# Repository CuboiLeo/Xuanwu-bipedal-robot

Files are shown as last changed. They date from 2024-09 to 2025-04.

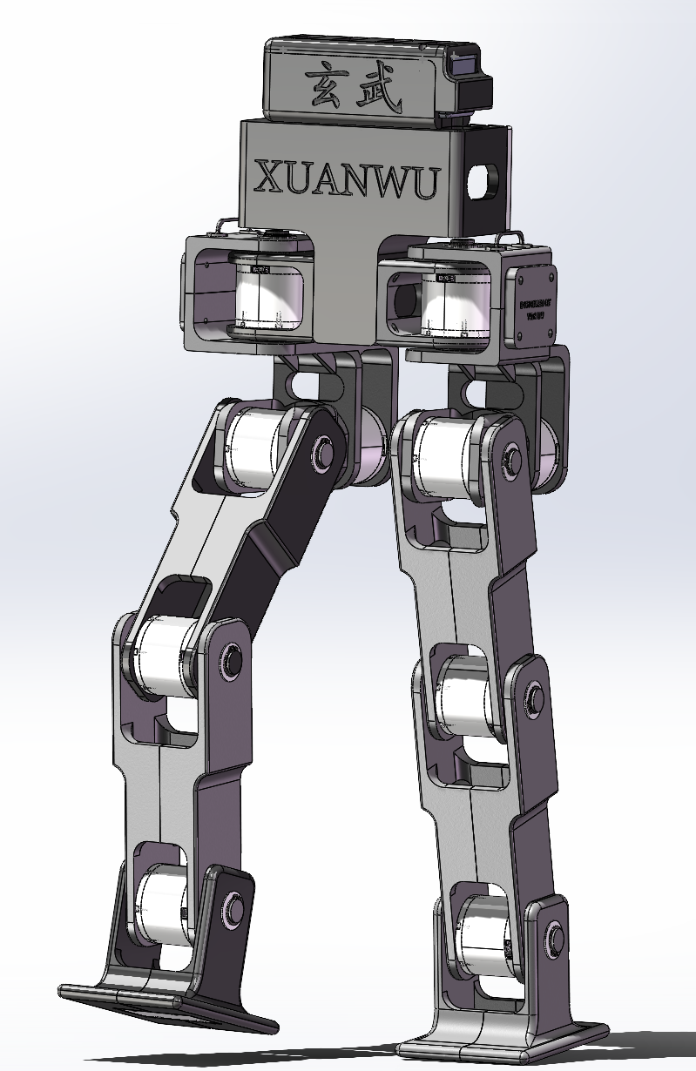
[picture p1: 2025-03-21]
media/image/CAD/Xuanwu v3.png

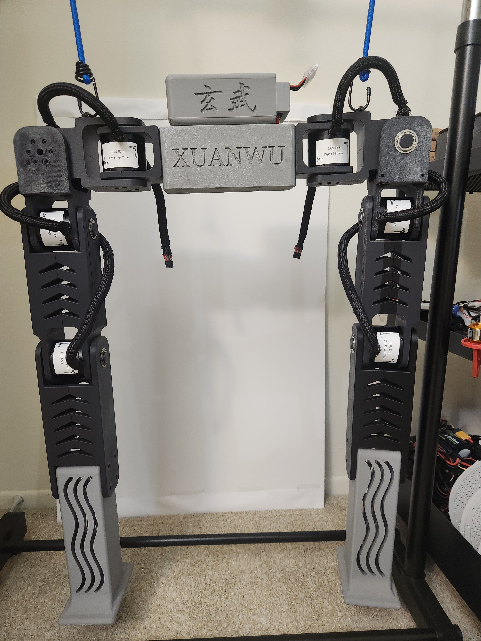
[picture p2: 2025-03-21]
media/image/Robot/Xuanwu v1.jpg

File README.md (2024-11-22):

# Xuanwu-bipedal-robot

This is an open-source bipedal robot project created by Yuxi Liu, aim to serve as a platform for testing various control algorithms

## Project hierarchy

This project contains three subfolders

- CAD - contains CAD files for parts of the robot, see CAD/README.md for detailed BoM and assembly guide
- source_code - contains code that the robot runs, see source_code/README.md for detailed introduction of code base structure
- media - contains media files such as video snippet of the robot, see media/README.md for more details

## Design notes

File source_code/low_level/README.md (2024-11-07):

# This folder is for the STM32H723 dev board

## IMPORTANT - If the project is regenerated using STM32CubeMX
You will see many errors if you rebuild the project in Keil, this is because STM32CubeMX uses RVDS for freeRTOS. To fix this, follow the following steps
1. Copy the GCC folder at the current directory
2. Paste it under ./Xuanwu_bipedal_robot/Middlewares/Third_Party/FreeRTOS/Source/portable, where you will see the STM32CubeMX generated RVDS and MemMang folders
3. Go to Keil, on the project tree on the left, find the last port.c file under Middlewares/FreeRTOS folder, right click and remove it
4. Go to Options for Target (magic wand icon in the tools menu), under C/C++, remove the RVDS/ARM_CM4F folder from the Include Paths
5. Build the project, there should (hopefully) be no more errors

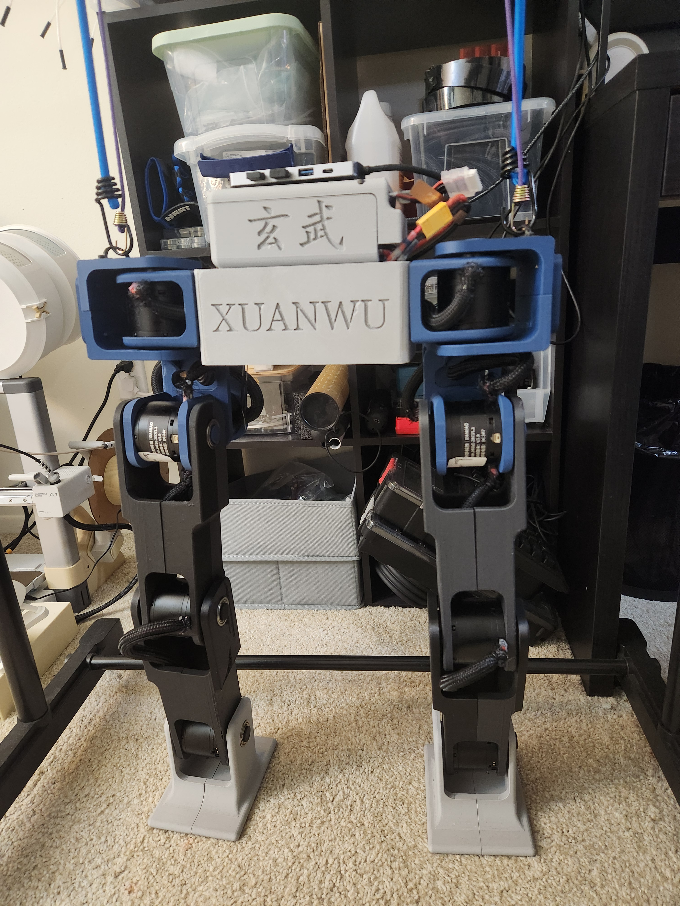
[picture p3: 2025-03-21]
media/image/Robot/Xuanwu v2.jpg

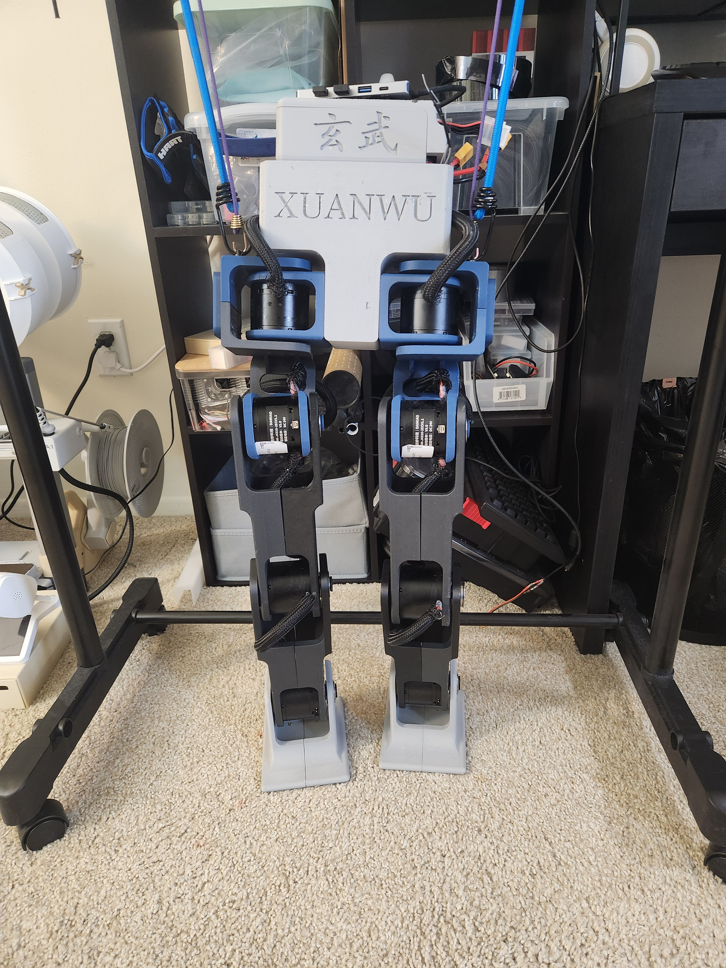
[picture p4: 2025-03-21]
media/image/Robot/Xuanwu v3.jpg

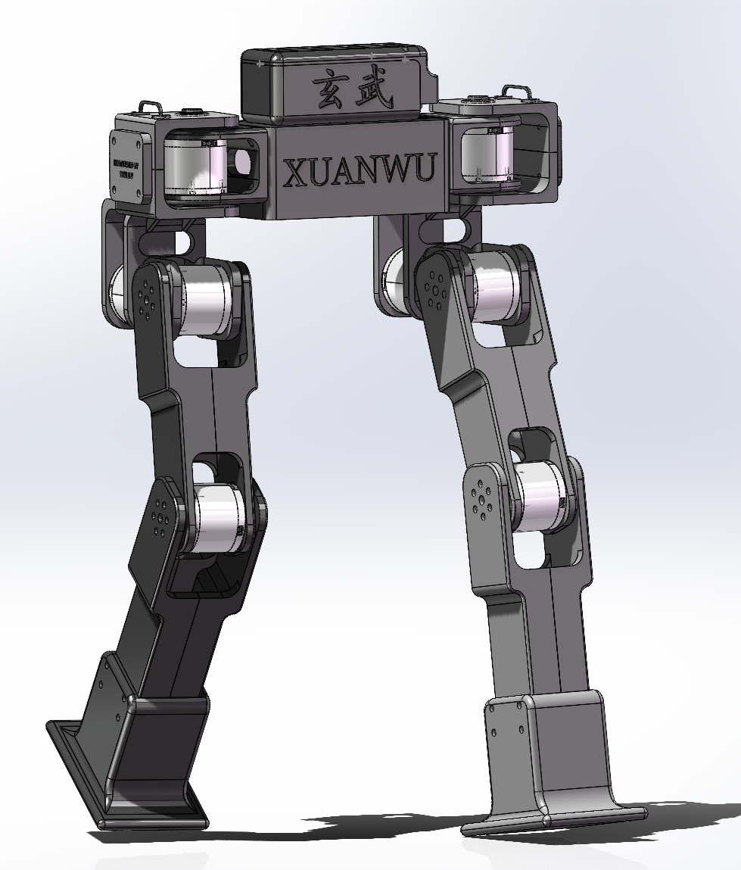
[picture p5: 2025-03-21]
media/image/CAD/Xuanwu v2.png

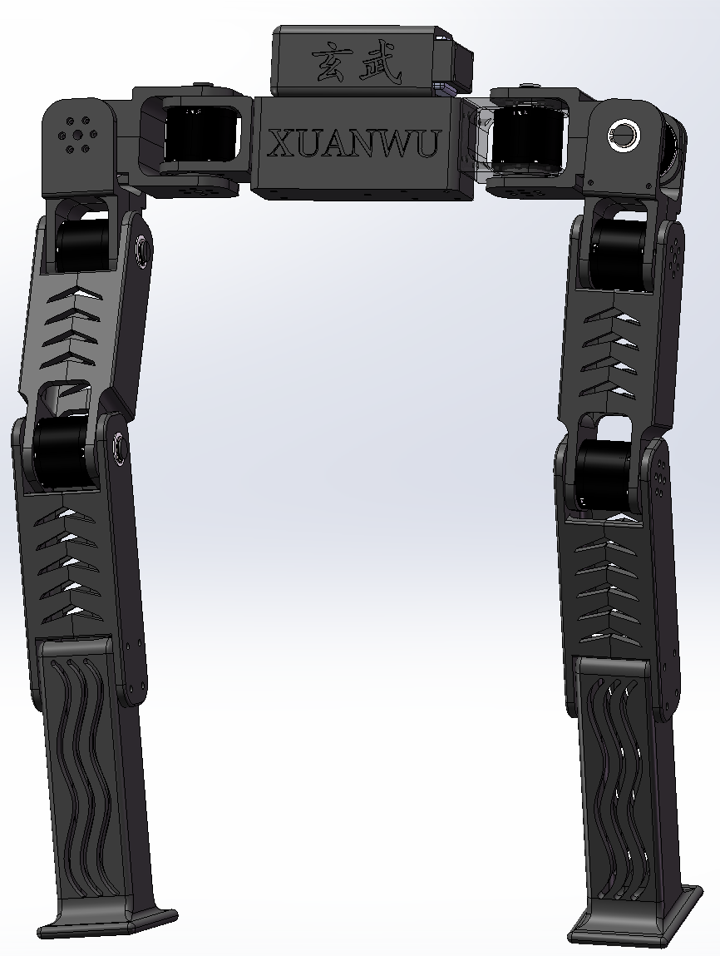
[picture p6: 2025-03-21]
media/image/CAD/Xuanwu v1.png

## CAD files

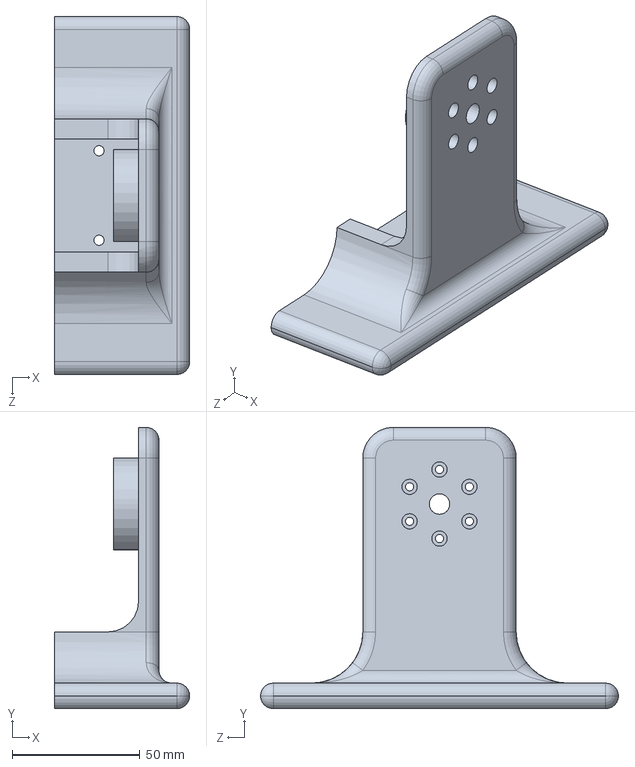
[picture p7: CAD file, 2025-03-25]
CAD/Leg/Divided Parts for Printing/DM-J4310 Foot Connector 1.SLDPRT
52.9 x 110.0 x 140.0 mm

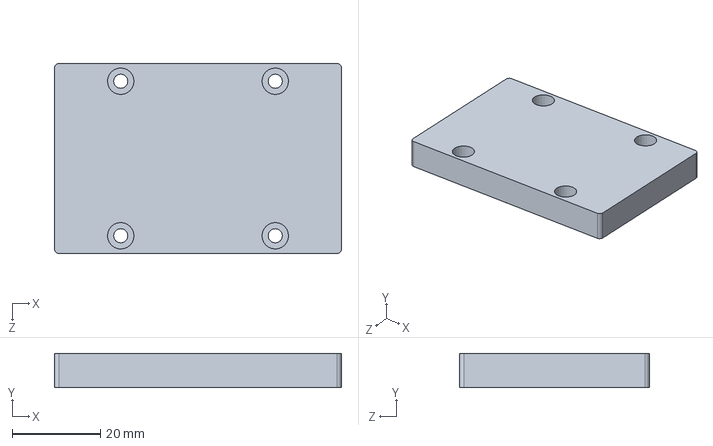
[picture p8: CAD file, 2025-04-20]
CAD/Leg/DM-J4310 Foot Joint Board.SLDPRT
65.0 x 7.80 x 43.0 mm

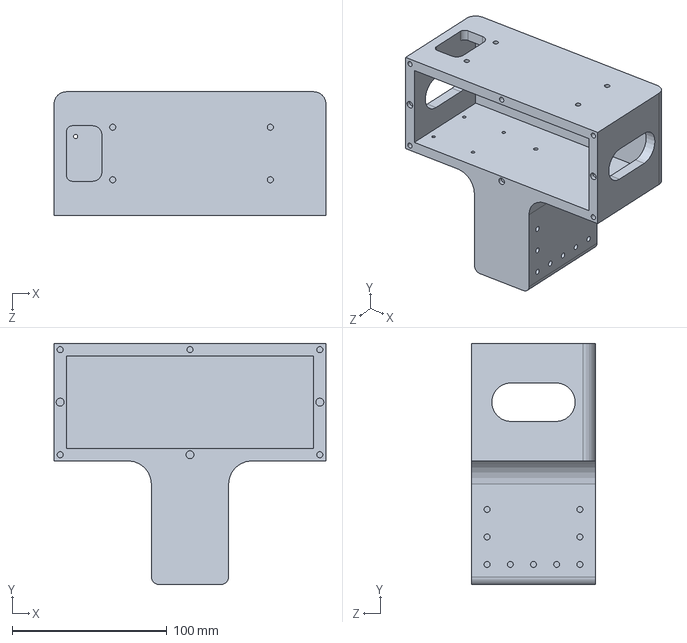
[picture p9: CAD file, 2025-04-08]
CAD/Main Control/Central Connector Module.SLDPRT
176.0 x 156.0 x 80.0 mm

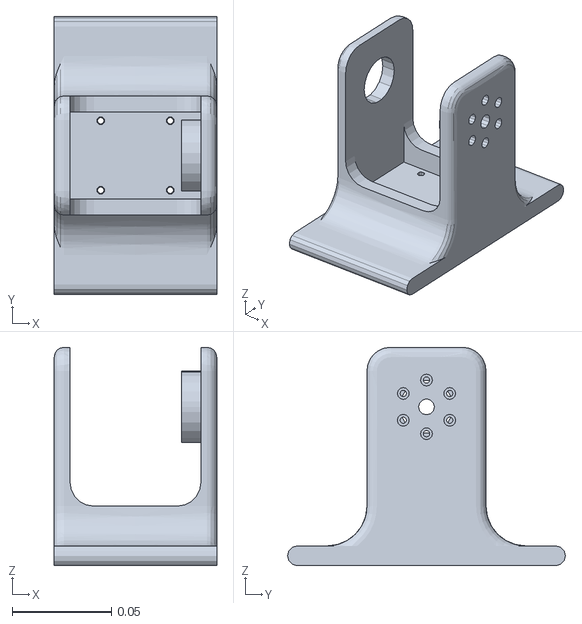
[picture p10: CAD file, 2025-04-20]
source_code/simulation/model/meshes/link_5.STL
0.0819 x 0.14 x 0.11

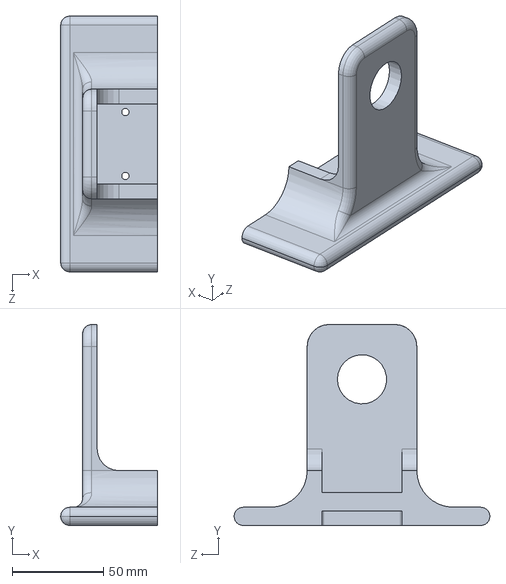
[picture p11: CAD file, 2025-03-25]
CAD/Leg/Divided Parts for Printing/DM-J4310 Foot Connector 2.SLDPRT
52.9 x 110.0 x 140.0 mm

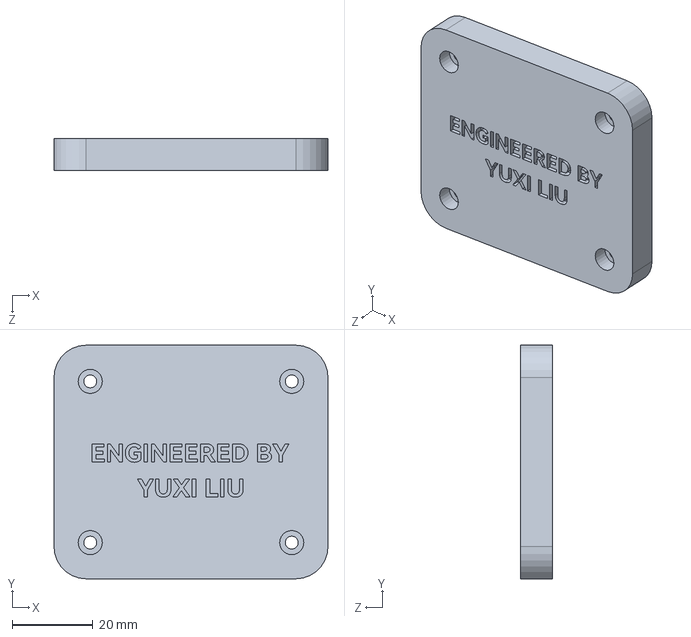
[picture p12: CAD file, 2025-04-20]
CAD/Leg/DM-J4310 Hip Roll Joint Board.SLDPRT
68.0 x 58.0 x 8.00 mm

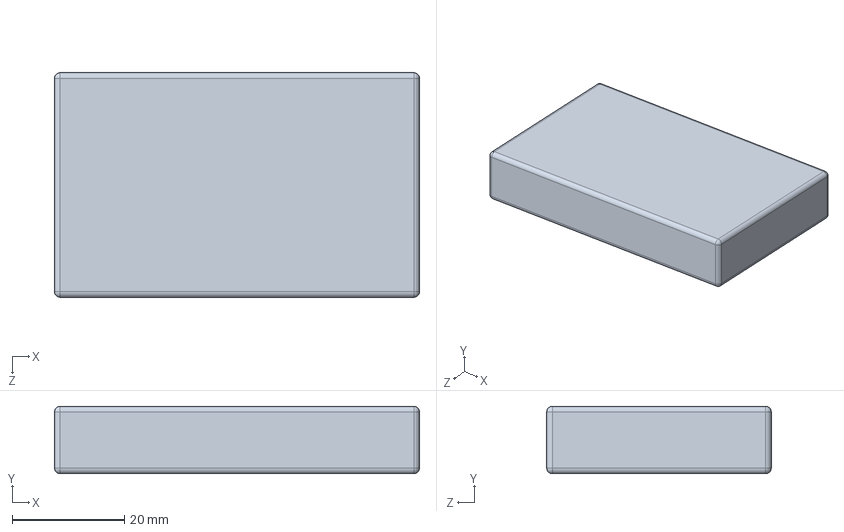
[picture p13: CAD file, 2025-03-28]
CAD/Main Control/Wireless Debugger.SLDPRT
65.0 x 12.0 x 40.0 mm

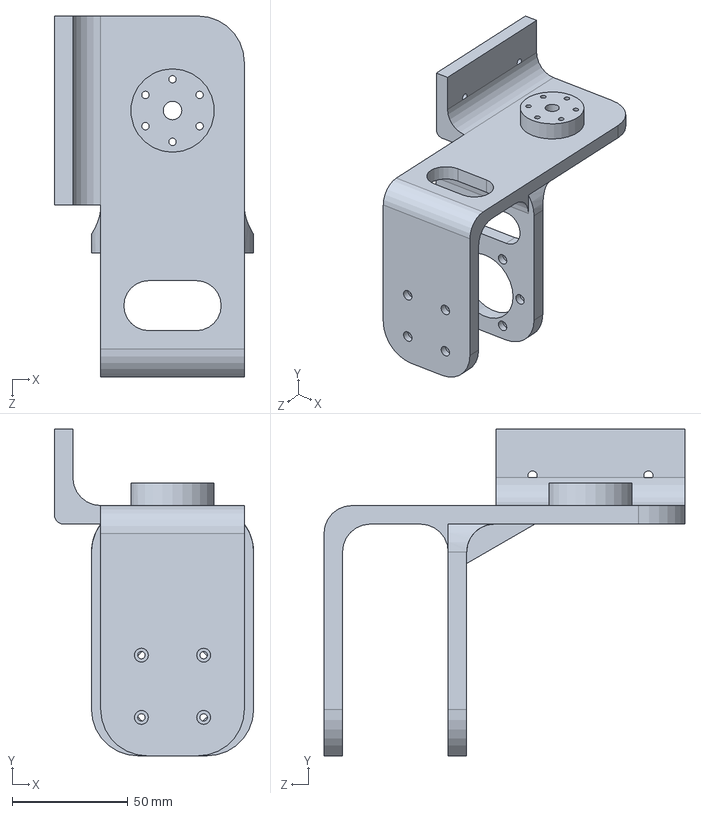
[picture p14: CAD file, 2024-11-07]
CAD/Leg/Divided Parts for Printing/DM-J4310 Hip Roll Connector Right 2.SLDPRT
86.0 x 140.9 x 155.8 mm

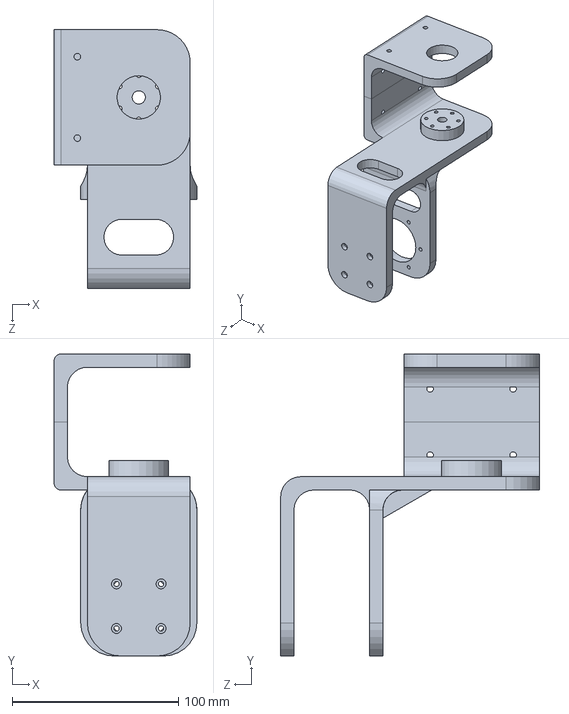
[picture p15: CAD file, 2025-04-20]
CAD/Leg/DM-J4310 Hip Roll Connector Right.SLDPRT
86.0 x 181.9 x 155.8 mm

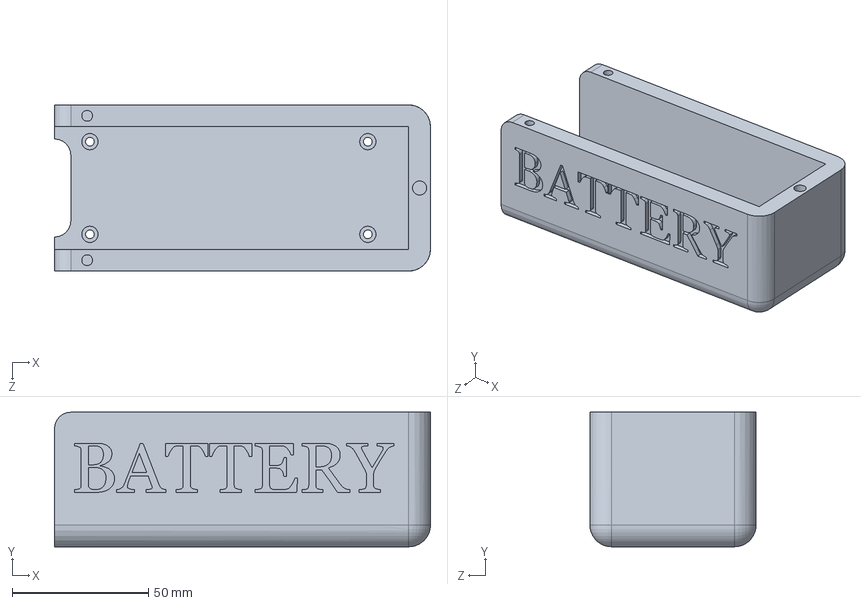
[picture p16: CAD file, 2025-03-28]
CAD/Main Control/Battery Case.SLDPRT
138.0 x 49.4 x 61.0 mm

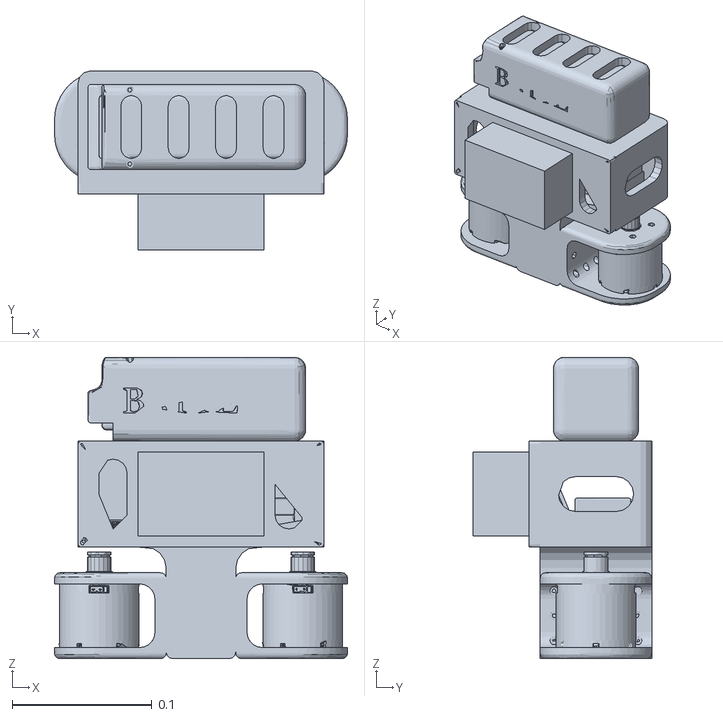
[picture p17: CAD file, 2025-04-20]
source_code/simulation/model/meshes/base_link.STL
0.21 x 0.128 x 0.216

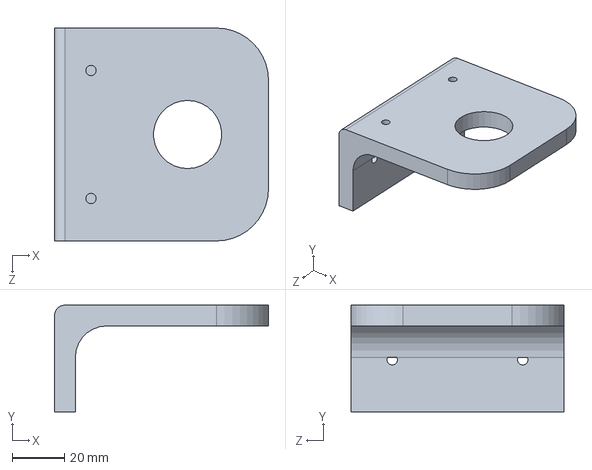
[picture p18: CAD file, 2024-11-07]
CAD/Leg/Divided Parts for Printing/DM-J4310 Hip Roll Connector Right 1.SLDPRT
82.0 x 41.0 x 81.6 mm

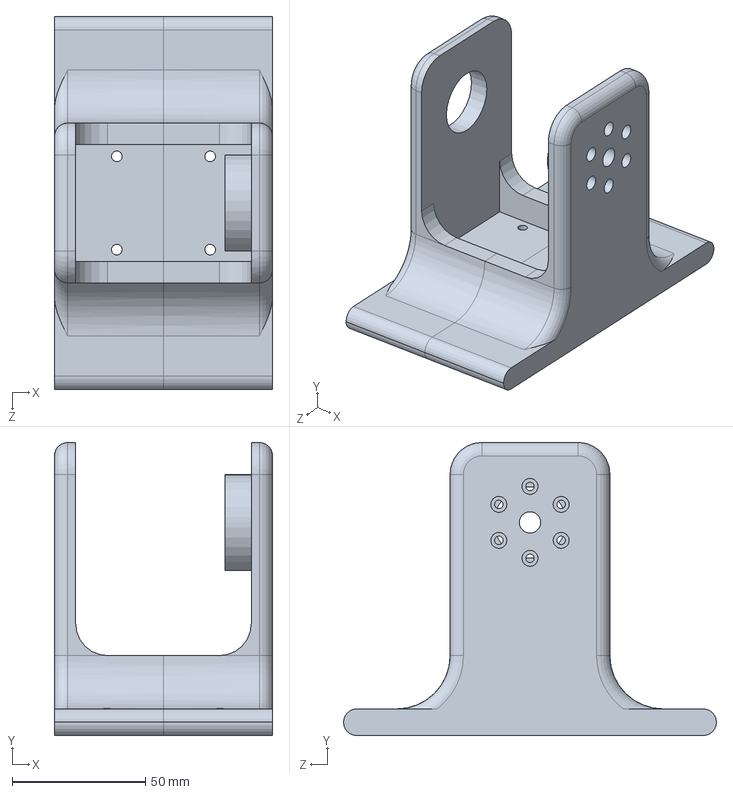
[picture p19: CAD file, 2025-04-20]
CAD/Leg/Foot Connector.SLDPRT
81.9 x 110.0 x 140.0 mm

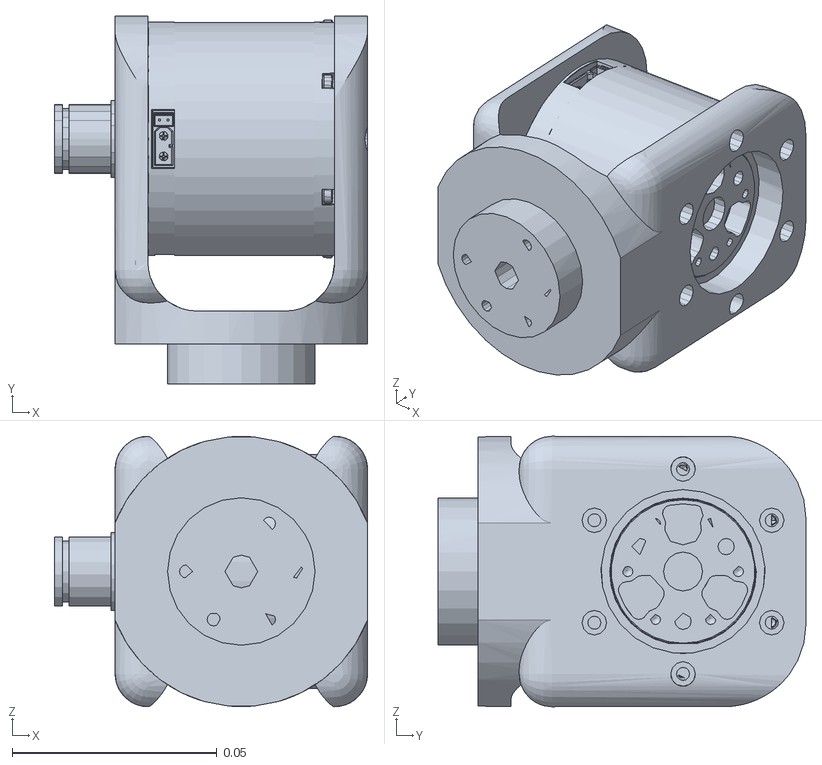
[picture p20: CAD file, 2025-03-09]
source_code/simulation/model/meshes/link_2.STL
0.0764 x 0.0898 x 0.066

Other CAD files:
CAD/Leg/Leg_Assem.SLDASM
source_code/simulation/model/meshes/link_10.STL
CAD/Main Control/CtrBoard Back Case.sldprt
CAD/Leg/Divided Parts for Printing/DM-J4310 Hip Roll Connector Left 1.SLDPRT
CAD/Leg/Bearing 17_26_5.SLDPRT
CAD/Leg/DM-J4310 Hip Pitch Connector.SLDPRT
CAD/Leg/DM-J4310 Hip Roll Connector Left.SLDPRT
CAD/Leg/DM-J4310 Hip Yaw Connector.SLDPRT
CAD/Leg/DM-J4310 Knee Pitch Connector.SLDPRT
CAD/Leg/Divided Parts for Printing/DM-J4310 Hip Roll Connector Left 2.SLDPRT
CAD/Leg/Divided Parts for Printing/DM-J4310 Knee Pitch Connector 1.SLDPRT
CAD/Leg/Divided Parts for Printing/DM-J4310 Knee Pitch Connector 2.SLDPRT
CAD/Leg/Hip Handle.SLDPRT
CAD/Main Control/6S Battery.SLDPRT
CAD/Main Control/Battery Case Cap.SLDPRT
CAD/Main Control/Central Connector Module Closing.SLDPRT
CAD/Main Control/CtrBoard Front Case.sldprt
CAD/Main Control/Orin Subs.SLDPRT
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

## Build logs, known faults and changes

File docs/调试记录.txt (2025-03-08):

2025/03/07 LIP模型
LIP模型假设腿无重量，实机调试时需要转移ZMP至支撑脚的convex hull后再迈下一步。
同时因最后输出为摆动腿的目标坐标，需要通过逆运动学得到期望的关节角度。然而双足的逆运动学（如果使用数值求解）常常只能近似，最终造成落点位置不精确。

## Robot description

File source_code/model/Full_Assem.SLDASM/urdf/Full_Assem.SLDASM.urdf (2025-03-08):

<?xml version="1.0" encoding="utf-8"?>
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
<robot name="Full_Assem.SLDASM">
  <link name="base_link">
    <inertial>
      <origin xyz="0.001 0 0.07" rpy="0 0 0" />
      <mass value="1.894" />
      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
    </inertial>
    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
  </link>
  <link name="link_1">
    <inertial>
      <origin xyz="-0.08 -0.06 -0.074" rpy="0 0 0" />
      <mass value="0.547" />
      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
    </inertial>
    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
  </link>
  <joint name="joint_1" type="revolute">
    <origin xyz="0 0 0" rpy="0 0 0" />
    <parent link="base_link" />
    <child link="link_1" />
    <axis xyz="0 0 1" />
    <limit lower="-0.5" upper="0.5" effort="7" velocity="12" />
  </joint>
  <link name="link_2">
    <inertial>
      <origin xyz="-0.073 -0.006 -0.111" rpy="0 0 0" />
      <mass value="0.378" />
      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
    </inertial>
    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
  </link>
  <joint name="joint_2" type="revolute">
    <origin xyz="0 0 0" rpy="0 0 0" />
    <parent link="link_1" />
    <child link="link_2" />
    <axis xyz="0 1 0" />
    <limit lower="-0.7" upper="0.7" effort="7" velocity="12" />
  </joint>
  <link name="link_3">
    <inertial>
      <origin xyz="-0.072 -0.001 -0.261" rpy="0 0 0" />
      <mass value="0.436" />
      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
    </inertial>
    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
  </link>
  <joint name="joint_3" type="revolute">
    <origin xyz="0 0 0" rpy="0 0 0" />
    <parent link="link_2" />
    <child link="link_3" />
    <axis xyz="1 0 0" />
    <limit lower="-0.25" upper="1.57" effort="7" velocity="12" />
  </joint>
  <link name="link_4">
    <inertial>
      <origin xyz="-0.072 -0.001 -0.441" rpy="0 0 0" />
      <mass value="0.436" />
      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
    </inertial>
    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
  </link>
  <joint name="joint_4" type="revolute">
    <origin xyz="0 0 0" rpy="0 0 0" />
    <parent link="link_3" />
    <child link="link_4" />
    <axis xyz="1 0 0" />
    <limit lower="-1.57" upper="1.57" effort="7" velocity="12" />
  </joint>
  <link name="link_5">
    <inertial>
      <origin xyz="-0.071 -0.001 -0.524" rpy="0 0 0" />
      <mass value="0.105" />
      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
    </inertial>
    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
  </link>
  <joint name="joint_5" type="revolute">
    <origin xyz="0 0 0" rpy="0 0 0" />
    <parent link="link_4" />
    <child link="link_5" />
    <axis xyz="1 0 0" />
    <limit lower="-1.57" upper="1.57" effort="7" velocity="12" />
  </joint>
  <link name="link_6">
    <inertial>
      <origin xyz="0.08 -0.06 -0.074" rpy="0 0 0" />
      <mass value="0.547" />
      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
    </inertial>
    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
  </link>
  <joint name="joint_6" type="revolute">
    <origin xyz="0 0 0" rpy="0 0 0" />
    <parent link="base_link" />
    <child link="link_6" />
    <axis xyz="0 0 1" />
    <limit lower="-0.5" upper="0.5" effort="7" velocity="12" />
  </joint>
  <link name="link_7">
    <inertial>
      <origin xyz="0.073 -0.006 -0.111" rpy="0 0 0" />
      <mass value="0.378" />
      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
    </inertial>
    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
  </link>
  <joint name="joint_7" type="revolute">
    <origin xyz="0 0 0" rpy="0 0 0" />
    <parent link="link_6" />
    <child link="link_7" />
    <axis xyz="0 1 0" />
    <limit lower="-0.7" upper="0.7" effort="7" velocity="12" />
  </joint>
  <link name="link_8">
    <inertial>
      <origin xyz="0.072 -0.001 -0.261" rpy="0 0 0" />
      <mass value="0.436" />
      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
    </inertial>
    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
  </link>
  <joint name="joint_8" type="revolute">
    <origin xyz="0 0 0" rpy="0 0 0" />
    <parent link="link_7" />
    <child link="link_8" />
    <axis xyz="1 0 0" />
    <limit lower="-0.25" upper="1.57" effort="7" velocity="12" />
  </joint>
  <link name="link_9">
    <inertial>
      <origin xyz="0.072 -0.001 -0.441" rpy="0 0 0" />
      <mass value="0.436" />
      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
    </inertial>
    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
  </link>
  <joint name="joint_9" type="revolute">
    <origin xyz="0 0 0" rpy="0 0 0" />
    <parent link="link_8" />
    <child link="link_9" />
    <axis xyz="1 0 0" />
    <limit lower="-1.57" upper="1.57" effort="7" velocity="12" />
  </joint>
  <link name="link_10">
    <inertial>
      <origin xyz="0.071 -0.001 -0.524" rpy="0 0 0" />
      <mass value="0.105" />
      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
    </inertial>
    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
  </link>
  <joint name="joint_10" type="revolute">
    <origin xyz="0 0 0" rpy="0 0 0" />
    <parent link="link_9" />
    <child link="link_10" />
    <axis xyz="1 0 0" />
    <limit lower="-1.57" upper="1.57" effort="7" velocity="12" />
  </joint>
</robot>

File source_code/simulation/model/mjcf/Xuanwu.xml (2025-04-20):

<mujoco model="Xuanwu">
  <option>
    <flag multiccd="enable"/>
  </option>
  <compiler angle="radian" meshdir="../meshes/" eulerseq="zyx"/>
  <size njmax="500" nconmax="100" />
  <option timestep="0.001" iterations="50" solver="PGS" gravity="0 0 -9.81" noslip_iterations="20">
  <flag sensornoise="enable" frictionloss="enable"/>
  </option>
  <default>
      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
  </default>
  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

  <worldbody>
    <light directional="true" diffuse=".4 .4 .4" specular="0.1 0.1 0.1" pos="0 0 5.0" dir="0 0 -1" castshadow="false"/>
    <light directional="true" diffuse=".6 .6 .6" specular="0.2 0.2 0.2" pos="0 0 4" dir="0 0 -1"/>
    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
    
    <body name="base_link" pos="0 0 0.556">
      <freejoint/>
      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
      <inertial pos="0.000934 -0.004880 0.069827" mass="2.016243" diaginertia="0.0251293 0.0206152 0.00691741"/>
      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
      <body name="link_1" pos="-0.073035 -1.4472E-05 -0.00095242" quat="1 0 0 0">
        <inertial pos="-0.006856 -0.062152 -0.076118" mass="0.504" diaginertia="0.00703726 0.0069965 0.000427238"/>
        <joint name="joint_1" pos="0 0 0" axis="0 0 1" range="-0.5 0.5" damping="0.01" frictionloss="0.01" armature="0.01" limited="true"/>
        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
        <body name="link_2" pos="4.9294E-05 -0.083183 -0.11003" quat="1 0 0 0">
          <inertial pos="-0.000218 0.076679 0.000024" mass="0.390" diaginertia="0.002479 0.00246102 0.000115979"/>
          <joint name="joint_2" pos="0 0 0" axis="0 1 0" range="-0.7 0.7" damping="0.01" frictionloss="0.01" armature="0.01" limited="true"/>
          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
          <body name="link_3" pos="0.00098795 0.082032 2.035E-05" quat="1 0 0 0">
            <inertial pos="-0.000371 -0.000049 -0.144385" mass="0.481" diaginertia="0.011859 0.0117753 0.000262696"/>
            <joint name="joint_3" pos="0 0 0" axis="1 0 0" range="-0.25 1.57" damping="0.01" frictionloss="0.01" armature="0.01" limited="true"/>
            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
            <body name="link_4" pos="5E-05 -5.7742E-05 -0.17996" quat="1 0 0 0">
              <inertial pos="-0.000371 0.000032 -0.144426" mass="0.481" diaginertia="0.011865 0.0117813 0.000262697"/>
              <joint name="joint_4" pos="0 0 0" axis="1 0 0" range="-1.57 1.57" damping="0.01" frictionloss="0.01" armature="0.01" limited="true"/>
              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
              <body name="link_5" pos="5E-05 3.7392E-05 -0.18" quat="1 0 0 0">
                <inertial pos="0.000400 -0.000014 -0.053536" mass="0.122" diaginertia="0.000567099 0.000555 0.000201901"/>
                <joint name="joint_5" pos="0 0 0" axis="1 0 0" range="-1.57 1.57" damping="0.01" frictionloss="0.01" armature="0.01" limited="true"/>
                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
              </body>
            </body>
          </body>
        </body>
      </body>
      <body name="link_6" pos="0.073035 1.4472E-05 -0.00095242" quat="1 0 0 0">
        <inertial pos="0.006873 -0.062180 -0.076118" mass="0.504" diaginertia="0.00703965 0.00699844 0.000425911"/>
        <joint name="joint_6" pos="0 0 0" axis="0 0 1" range="-0.5 0.5" damping="0.01" frictionloss="0.01" armature="0.01" limited="true"/>
        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
        <body name="link_7" pos="-2.035E-05 -0.083212 -0.11003" quat="1 0 0 0">
          <inertial pos="0.000189 0.076679 0.000046" mass="0.390" diaginertia="0.002479 0.00246102 0.000115984"/>
          <joint name="joint_7" pos="0 0 0" axis="0 1 0" range="-0.7 0.7" damping="0.01" frictionloss="0.01" armature="0.01" limited="true"/>
          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
          <body name="link_8" pos="-0.0010169 0.082032 4.9294E-05" quat="1 0 0 0"> 
            <inertial pos="0.000371 -0.000021 -0.144414" mass="0.481" diaginertia="0.011863 0.0117793 0.000262698"/>
            <joint name="joint_8" pos="0 0 0" axis="1 0 0" range="-0.25 1.57" damping="0.01" frictionloss="0.01" armature="0.01" limited="true"/>
            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
            <body name="link_9" pos="-5E-05 -1.1901E-05 -0.17998" quat="1 0 0 0">
              <inertial pos="0.000371 -0.000001 -0.144439" mass="0.481" diaginertia="0.011867 0.0117833 0.000262698"/>
              <joint name="joint_9" pos="0 0 0" axis="1 0 0" range="-1.57 1.57" damping="0.01" frictionloss="0.01" armature="0.01" limited="true"/>
              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
              <body name="link_10" pos="-5E-05 1.1901E-05 -0.18002" quat="1 0 0 0">
                <inertial pos="-0.000400 -0.000035 -0.053516" mass="0.122" diaginertia="0.000566099 0.000554 0.000201901"/>
                <joint name="joint_10" pos="0 0 0" axis="1 0 0" range="-1.57 1.57" damping="0.01" frictionloss="0.01" armature="0.01" limited="true"/>
                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
              </body>
            </body>
          </body>
        </body>
      </body>
    </body>
  </worldbody>
  <actuator>
    <motor gear="1" joint="joint_1" name="motor_1" ctrllimited="true" ctrlrange='-7 7'/>
    <motor gear="1" joint="joint_2" name="motor_2" ctrllimited="true" ctrlrange='-7 7'/>
    <motor gear="1" joint="joint_3" name="motor_3" ctrllimited="true" ctrlrange='-7 7'/>
    <motor gear="1" joint="joint_4" name="motor_4" ctrllimited="true" ctrlrange='-7 7'/>
    <motor gear="1" joint="joint_5" name="motor_5" ctrllimited="true" ctrlrange='-7 7'/>
    <motor gear="1" joint="joint_6" name="motor_6" ctrllimited="true" ctrlrange='-7 7'/>
    <motor gear="1" joint="joint_7" name="motor_7" ctrllimited="true" ctrlrange='-7 7'/>
    <motor gear="1" joint="joint_8" name="motor_8" ctrllimited="true" ctrlrange='-7 7'/>
    <motor gear="1" joint="joint_9" name="motor_9" ctrllimited="true" ctrlrange='-7 7'/>
    <motor gear="1" joint="joint_10" name="motor_10" ctrllimited="true" ctrlrange='-7 7'/>
  </actuator>
  <sensor>
    <actuatorpos name="joint_1_pos" actuator="motor_1"/>
    <actuatorpos name="joint_2_pos" actuator="motor_2"/>
    <actuatorpos name="joint_3_pos" actuator="motor_3"/>
    <actuatorpos name="joint_4_pos" actuator="motor_4"/>
    <actuatorpos name="joint_5_pos" actuator="motor_5"/>
    <actuatorpos name="joint_6_pos" actuator="motor_6"/>
    <actuatorpos name="joint_7_pos" actuator="motor_7"/>
    <actuatorpos name="joint_8_pos" actuator="motor_8"/>
    <actuatorpos name="joint_9_pos" actuator="motor_9"/>
    <actuatorpos name="joint_10_pos" actuator="motor_10"/>

    <actuatorvel name="joint_1_vel" actuator="motor_1"/>
    <actuatorvel name="joint_2_vel" actuator="motor_2"/>
    <actuatorvel name="joint_3_vel" actuator="motor_3"/>
    <actuatorvel name="joint_4_vel" actuator="motor_4"/>
    <actuatorvel name="joint_5_vel" actuator="motor_5"/>
    <actuatorvel name="joint_6_vel" actuator="motor_6"/>
    <actuatorvel name="joint_7_vel" actuator="motor_7"/>
    <actuatorvel name="joint_8_vel" actuator="motor_8"/>
    <actuatorvel name="joint_9_vel" actuator="motor_9"/>
    <actuatorvel name="joint_10_vel" actuator="motor_10"/>

    <actuatorfrc name="joint_1_frc" actuator="motor_1"/>
    <actuatorfrc name="joint_2_frc" actuator="motor_2"/>
    <actuatorfrc name="joint_3_frc" actuator="motor_3"/>
    <actuatorfrc name="joint_4_frc" actuator="motor_4"/>
    <actuatorfrc name="joint_5_frc" actuator="motor_5"/>
    <actuatorfrc name="joint_6_frc" actuator="motor_6"/>
    <actuatorfrc name="joint_7_frc" actuator="motor_7"/>
    <actuatorfrc name="joint_8_frc" actuator="motor_8"/>
    <actuatorfrc name="joint_9_frc" actuator="motor_9"/>
    <actuatorfrc name="joint_10_frc" actuator="motor_10"/>

    <framequat name='orientation' objtype='site' noise='0.001' objname='imu'/>
    <framepos name='position' objtype='site' noise='0.001' objname='imu'/>
    <gyro name='angular-velocity' site='imu' noise='0.005' cutoff='34.9'/>
    <velocimeter name='linear-velocity' site='imu' noise='0.001' cutoff='30'/>
    <accelerometer name='linear-acceleration' site='imu' noise='0.005' cutoff='157'/>
    <magnetometer name='magnetometer' site='imu'/>
  </sensor>
</mujoco>

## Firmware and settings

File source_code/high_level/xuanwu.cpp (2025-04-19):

#include <iostream>
#include <unistd.h>
#include <thread>
#include <mutex>
#include <condition_variable>
#include <chrono>
#include <sched.h>
#include <pthread.h>
#include "STM32_protocol.h"
#include "motor.h"
#include "IMU.h"
#include "command.h"
#include "robot.h"
#include "kinematics.h"
#include "dynamics.h"
#include "controls.h"
#include "walking_patterns.h"
#include "estimations.h"
#include "data_exporter.h"
#include "RL_inference.h"

// Shared data between threads
struct Shared_Data
{
    Motor motor;
    IMU imu;
    Command command;

    bool new_data = false;
};

Shared_Data shared_data;                // Global shared data
std::mutex shared_data_mutex;           // Mutex for shared data
std::condition_variable shared_data_cv; // Condition variable for shared data
STM32 stm32;                            // STM32 object for CAN communication
CAN can("can0");                        // CAN object for communication

// Thread function declarations
void CAN_receive_thread();
void CAN_send_thread();
void compute_thread();
void set_thread_realtime(std::thread &thread, int priority);
void pinThreadToCore(std::thread &thr, int core_id);

int main()
{
    std::thread CAN_receive(CAN_receive_thread);
    std::thread compute(compute_thread);
    std::thread CAN_send(CAN_send_thread);

    set_thread_realtime(CAN_receive, 99);
    set_thread_realtime(compute, 99);
    set_thread_realtime(CAN_send, 99);

    pinThreadToCore(CAN_receive, 1);
    pinThreadToCore(compute, 2);
    pinThreadToCore(CAN_send, 3);

    CAN_receive.join();
    compute.join();
    CAN_send.join();

    return 0;
}

void compute_thread()
{
    Robot robot;                                                                    // Robot object for robot state
    Kinematics kinematics;                                                          // Kinematics object for kinematics computation
    Dynamics dynamics;                                                              // Dynamics object for dynamics computation
    Controls controls;                                                              // Controls object for control computation
    Estimations estimations;                                                        // Estimation object for estimation computation
    Walking_Patterns walking_patterns;                                              // Walking patterns object for walking pattern computation
    RL_Inference rl_inference("../../RL/trained_policy/flat_ground_walking_v1.pt"); // RL inference object for RL policy inference
    auto start = std::chrono::high_resolution_clock::now();
    auto next_cycle = std::chrono::steady_clock::now();

    while (true)
    {
        next_cycle += std::chrono::milliseconds(10); // 100 Hz

        std::unique_lock<std::mutex> lock(shared_data_mutex); // Lock the shared data
        shared_data_cv.wait(lock, []
                            { return shared_data.new_data; }); // Wait for new data
        shared_data.new_data = false;

        // Update the IMU data
        shared_data.imu.processData();

        // Set the leg act angles
        Joint_Angles left_act_angle = {shared_data.motor.getActPos(Left_Hip_Yaw), shared_data.motor.getActPos(Left_Hip_Roll), shared_data.motor.getActPos(Left_Hip_Pitch), shared_data.motor.getActPos(Left_Knee_Pitch), shared_data.motor.getActPos(Left_Ankle_Pitch)};
        Joint_Angles right_act_angle = {shared_data.motor.getActPos(Right_Hip_Yaw), shared_data.motor.getActPos(Right_Hip_Roll), shared_data.motor.getActPos(Right_Hip_Pitch), shared_data.motor.getActPos(Right_Knee_Pitch), shared_data.motor.getActPos(Right_Ankle_Pitch)};
        robot.setLegActAngles(left_act_angle, right_act_angle);

        // Set the leg act velocities
        Joint_Velocities left_act_vel = {shared_data.motor.getActVel(Left_Hip_Yaw), shared_data.motor.getActVel(Left_Hip_Roll), shared_data.motor.getActVel(Left_Hip_Pitch), shared_data.motor.getActVel(Left_Knee_Pitch), shared_data.motor.getActVel(Left_Ankle_Pitch)};
        Joint_Velocities right_act_vel = {shared_data.motor.getActVel(Right_Hip_Yaw), shared_data.motor.getActVel(Right_Hip_Roll), shared_data.motor.getActVel(Right_Hip_Pitch), shared_data.motor.getActVel(Right_Knee_Pitch), shared_data.motor.getActVel(Right_Ankle_Pitch)};
        robot.setLegActVel(left_act_vel, right_act_vel);

        // Set the leg act torques
        // Joint_Torques left_act_torque = {shared_data.motor.getActTor(Left_Hip_Yaw), shared_data.motor.getActTor(Left_Hip_Roll), shared_data.motor.getActTor(Left_Hip_Pitch), shared_data.motor.getActTor(Left_Knee_Pitch), shared_data.motor.getActTor(Left_Ankle_Pitch)};
        // Joint_Torques right_act_torque = {shared_data.motor.getActTor(Right_Hip_Yaw), shared_data.motor.getActTor(Right_Hip_Roll), shared_data.motor.getActTor(Right_Hip_Pitch), shared_data.motor.getActTor(Right_Knee_Pitch), shared_data.motor.getActTor(Right_Ankle_Pitch)};
        // robot.setLegActTorque(left_act_torque, right_act_torque);

        // Compute the center of mass position
        // Position CoM_pos = kinematics.computeCoMPos({robot.getLegActAngles(LEFT_LEG_ID), robot.getLegActAngles(RIGHT_LEG_ID)}, shared_data.imu.getRotationMatrix());
        // robot.setCoMActPos(CoM_pos);

        // Compute the center of mass acceleration
        // Acceleration CoM_accel = dynamics.computeCoMAccel(robot.getCoMActPos(), shared_data.imu.getAccel(), shared_data.imu.getGyro(), shared_data.imu.getGyroDot());
        // robot.setCoMActAccel(CoM_accel);

        // Compute the zero moment point position
        // Position ZMP_pos = dynamics.computeZMPPos(robot.getCoMActPos(), robot.getCoMActAccel());
        // robot.setZMPActPos(ZMP_pos);
        // std::cout << "CoM Position: " << CoM_pos.x << " " << CoM_pos.y << " " << CoM_pos.z << std::endl;
        // std::cout << "ZMP Position: " << ZMP_pos.x << " " << ZMP_pos.y << std::endl;

        // Estimate the center of mass states
        // estimations.estimateCoMStates(shared_data.imu.getVel(), shared_data.imu.getAccel());
        // Velocity estimated_CoM_vel = estimations.getEstimatedCoMVel();

        // Compute the foot forward kinematics
        // Pose left_act_pose = trans_to_pose(kinematics.computeFootFK(robot.getLegActAngles(LEFT_LEG_ID), LEFT_LEG_ID));
        // Pose right_act_pose = trans_to_pose(kinematics.computeFootFK(robot.getLegActAngles(RIGHT_LEG_ID), RIGHT_LEG_ID));
        // robot.setFootActPose(left_act_pose, right_act_pose);
        // std::cout << "Left Foot Pose: " << left_act_pose.position.x << " " << left_act_pose.position.y << " " << left_act_pose.position.z << " " << left_act_pose.orientation.roll << " " << left_act_pose.orientation.pitch << " " << left_act_pose.orientation.yaw << std::endl;
        // std::cout << "Right Foot Pose: " << right_act_pose.position.x << " " << right_act_pose.position.y << " " << right_act_pose.position.z << " " << right_act_pose.orientation.roll << " " << right_act_pose.orientation.pitch << " " << right_act_pose.orientation.yaw << std::endl;

        // Set the foot reference pose with walking pattern generator
        // Pose_Two_Foots foot_ref_poses = walking_patterns.gaitPlanner(robot.getCoMActPos(), estimations.getEstimatedCoMVel(), {robot.getFootActPose(LEFT_LEG_ID), robot.getFootActPose(RIGHT_LEG_ID)}, shared_data.imu.getEuler().roll);
        // robot.setFootRefPose(foot_ref_poses.left, foot_ref_poses.right);

        // Pose left_ref_pose = {{-L1, -0.001, -0.55}, {0, 0, 0}};
        // Pose right_ref_pose = {{L1, -0.001, -0.55}, {0, 0, 0}};
        // robot.setFootRefPose(left_ref_pose, right_ref_pose);

        // Compute the inverse kinematics
        // Joint_Angles left_ref_angle = kinematics.computeFootIK(robot.getFootActPose(LEFT_LEG_ID), robot.getFootRefPose(LEFT_LEG_ID), robot.getLegActAngles(LEFT_LEG_ID), LEFT_LEG_ID);
        // Joint_Angles right_ref_angle = kinematics.computeFootIK(robot.getFootActPose(RIGHT_LEG_ID), robot.getFootRefPose(RIGHT_LEG_ID), robot.getLegActAngles(LEFT_LEG_ID), RIGHT_LEG_ID);
        // robot.setLegRefAngles(left_ref_angle, right_ref_angle);
        // std::cout << "Left Angles:  " << left_ref_angle.hip_yaw << " | " << left_ref_angle.hip_roll << " | " << left_ref_angle.hip_pitch << " | " << left_ref_angle.knee_pitch << " | " << left_ref_angle.ankle_pitch << std::endl;
        // std::cout << "Right Angles: " << right_ref_angle.hip_yaw << " | " << right_ref_angle.hip_roll << " | " << right_ref_angle.hip_pitch << " | " << right_ref_angle.knee_pitch << " | " << right_ref_angle.ankle_pitch << std::endl;

        // Set the leg reference velocities
        // robot.setLegRefVel({0, 0, 0, 0, 0}, {0, 0, 0, 0, 0});

        // Set the leg reference torques
        // double gait_phase = walking_patterns.getGaitPhase();
        // int step_counter = walking_patterns.getStepCounter();
        // Joint_Torques left_ref_torque;
        // Joint_Torques right_ref_torque;
        // if (gait_phase < walking_patterns.Tdbl)
        // {
        //     left_ref_torque = dynamics.computeGRFTorques({0, 0, MT * GRAVITY / 2, 0, MT * GRAVITY / 2 * L1, 0}, robot.getLegActAngles(LEFT_LEG_ID), LEFT_LEG_ID);
        //     right_ref_torque = dynamics.computeGRFTorques({0, 0, MT * GRAVITY / 2, 0, -MT * GRAVITY / 2 * L1, 0}, robot.getLegActAngles(RIGHT_LEG_ID), RIGHT_LEG_ID);
        // }
        // else
        // {
        //     if (step_counter % 2 == 0)
        //     {
        //         left_ref_torque = {0, 0, 0, 0, 0};
        //         right_ref_torque = dynamics.computeGRFTorques({0, 0, MT * GRAVITY, 0, -MT * GRAVITY * L1, 0}, robot.getLegActAngles(RIGHT_LEG_ID), RIGHT_LEG_ID);
        //     }
        //     else
        //     {
        //         left_ref_torque = dynamics.computeGRFTorques({0, 0, MT * GRAVITY, 0, MT * GRAVITY * L1, 0}, robot.getLegActAngles(LEFT_LEG_ID), LEFT_LEG_ID);
        //         right_ref_torque = {0, 0, 0, 0, 0};
        //     }
        // }
        // robot.setLegRefTorque(left_ref_torque, right_ref_torque);
        // robot.setLegRefTorque({0, 0, 0, 0, 0}, {0, 0, 0, 0, 0});
        auto end = std::chrono::high_resolution_clock::now();
        std::chrono::duration<double> elapsed = end - start;
        // std::cout << "Current time: " << elapsed.count() << " seconds" << std::endl;

        std::vector<float> cmd = {(float)shared_data.command.getLinearVel().x, (float)shared_data.command.getLinearVel().y, (float)shared_data.command.getAngularVel().z};
        std::vector<float> q = {(float)left_act_angle.hip_yaw, (float)left_act_angle.hip_roll, (float)left_act_angle.hip_pitch, (float)left_act_angle.knee_pitch, (float)left_act_angle.ankle_pitch, (float)right_act_angle.hip_yaw, (float)right_act_angle.hip_roll, (float)right_act_angle.hip_pitch, (float)right_act_angle.knee_pitch, (float)right_act_angle.ankle_pitch};
        std::vector<float> dq = {(float)left_act_vel.hip_yaw, (float)left_act_vel.hip_roll, (float)left_act_vel.hip_pitch, (float)left_act_vel.knee_pitch, (float)left_act_vel.ankle_pitch, (float)right_act_vel.hip_yaw, (float)right_act_vel.hip_roll, (float)right_act_vel.hip_pitch, (float)right_act_vel.knee_pitch, (float)right_act_vel.ankle_pitch};
        Eigen::Vector3d gyro = shared_data.imu.getGyro();
        std::vector<float> omega = {(float)gyro(0), (float)gyro(1), (float)gyro(2)};
        std::vector<float> eul_ang = {(float)shared_data.imu.getEuler().roll, (float)shared_data.imu.getEuler().pitch, (float)shared_data.imu.getEuler().yaw};

        std::vector<float> target_q = rl_inference.infer(elapsed.count(), cmd, q, dq, omega, eul_ang);
        Joint_Angles left_ref_angle = {target_q[0], target_q[1], target_q[2], target_q[3], target_q[4]};
        Joint_Angles right_ref_angle = {target_q[5], target_q[6], target_q[7], target_q[8], target_q[9]};
        // float scale = 0.0f;
        // Joint_Angles left_ref_angle = {0.0 * sin(2 * PI * elapsed.count() / 0.64), 0.2 * sin(2 * PI * elapsed.count() / 0.64), scale * sin(2 * PI * elapsed.count() / 0.64) + 0.152f, -2.0f*scale* sin(2 * PI * elapsed.count() / 0.64) - 0.36f, scale * sin(2 * PI * elapsed.count() / 0.64) + 0.208f};
        // Joint_Angles right_ref_angle = {0, 0, 0, 0, 0};
        robot.setLegRefAngles(left_ref_angle, right_ref_angle);
        // std::cout << "Left Angles: " << left_ref_angle.hip_yaw << " | " << left_ref_angle.hip_roll << " | " << left_ref_angle.hip_pitch << " | " << left_ref_angle.knee_pitch << " | " << left_ref_angle.ankle_pitch << std::endl;
        // std::cout << "Right Angle: " << right_ref_angle.hip_yaw << " | " << right_ref_angle.hip_roll << " | " << right_ref_angle.hip_pitch << " | " << right_ref_angle.knee_pitch << " | " << right_ref_angle.ankle_pitch << std::endl;

        // Set the motor data
        robot.setMotorData(shared_data.motor);

        // Test the foot wrench computation (checked)
        // Wrench right_foot_wrench = dynamics.computeFootWrench(robot.getLegActTorque(RIGHT_LEG_ID), robot.getLegActAngles(RIGHT_LEG_ID), RIGHT_LEG_ID);

        // logDataToCSV(elapsed.count(), left_ref_angle.hip_yaw, left_ref_angle.hip_roll, left_ref_angle.hip_pitch, left_ref_angle.knee_pitch, left_ref_angle.ankle_pitch);
        // logDataToCSV(elapsed.count(),omega[0],omega[1],omega[2]);
        lock.unlock(); // Unlock the shared data
        std::this_thread::sleep_until(next_cycle);
    }
}

void CAN_receive_thread()
{
    auto start = std::chrono::high_resolution_clock::now();
    while (true)
    {
        stm32.receiveData(can); // Receive data from the STM32
        {
            std::lock_guard<std::mutex> lock(shared_data_mutex); // Lock the shared data
#ifdef USE_LITE_PACKAGE
            stm32.decodeDataLite(shared_data.motor, shared_data.imu, shared_data.command); // Decode the received data
#else
            stm32.decodeData(shared_data.motor, shared_data.imu, shared_data.command); // Decode the received data
#endif
            shared_data.new_data = true; // Set the new data flag
            shared_data_cv.notify_one(); // Notify the compute thread that new data is available
        }
        auto end = std::chrono::high_resolution_clock::now();
        std::chrono::duration<double> elapsed = end - start;
        // std::cout << "Current time: " << elapsed.count() << " seconds" << std::endl;
    }
}

void CAN_send_thread()
{
    auto start = std::chrono::high_resolution_clock::now();
    auto next_cycle = std::chrono::steady_clock::now();
    while (true)
    {
        next_cycle += std::chrono::milliseconds(1);
        {
            std::lock_guard<std::mutex> lock(shared_data_mutex); // Lock the shared data
#ifdef USE_LITE_PACKAGE
            stm32.encodeDataLite(shared_data.motor); // Encode the data to send
#else
            stm32.encodeData(shared_data.motor); // Encode the data to send
#endif
        }
        stm32.sendData(can); // Send the data to the STM32
        std::this_thread::sleep_until(next_cycle);

        auto end = std::chrono::high_resolution_clock::now();
        std::chrono::duration<double> elapsed = end - start;
        // std::cout << "Current time: " << elapsed.count() << " seconds" << std::endl;
    }
}

void set_thread_realtime(std::thread &thread, int priority)
{
    // Convert std::thread to pthread
    pthread_t native_handle = thread.native_handle();

    // Prepare the scheduling params
    sched_param sch_params;
    sch_params.sched_priority = priority;

    // Attempt to set the policy & priority
    int policy = SCHED_FIFO;
    int ret = pthread_setschedparam(native_handle, policy, &sch_params);
    if (ret != 0)
    {
        std::cerr << "Failed to set RT priority for thread. Errno: " << ret << std::endl;
    }
}

void pinThreadToCore(std::thread &thr, int core_id)
{
    // Prepare a CPU set
    cpu_set_t cpuset;
    CPU_ZERO(&cpuset);
    CPU_SET(core_id, &cpuset);

    // Convert std::thread to pthread
    pthread_t native_handle = thr.native_handle();

    // Call pthread_setaffinity_np
    int rc = pthread_setaffinity_np(native_handle, sizeof(cpu_set_t), &cpuset);
    if (rc != 0)
    {
        std::cerr << "Error calling pthread_setaffinity_np: "
                  << strerror(rc) << std::endl;
    }
    else
    {
        std::cout << "Pinned thread to core " << core_id << std::endl;
    }
}

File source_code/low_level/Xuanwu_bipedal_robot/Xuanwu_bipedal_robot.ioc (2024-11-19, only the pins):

Mcu.UserName=STM32H723VGTx
PA0.Signal=GPIO_Output
PA13(JTMS/SWDIO).Signal=DEBUG_JTMS-SWDIO
PA14(JTCK/SWCLK).Signal=DEBUG_JTCK-SWCLK
PA5.Signal=ADCx_INP19
PB1.Signal=S_TIM3_CH4
PB13.Signal=SPI2_SCK
PB15.GPIO_Label=BUZZER
PB15.Signal=S_TIM12_CH2
PB5.Signal=FDCAN2_RX
PB6.Signal=FDCAN2_TX
PC0.GPIO_Label=ACC_CS
PC0.Signal=GPIO_Output
PC1.Signal=SPI2_MOSI
PC12.Signal=UART5_TX
PC13.GPIO_Label=CAN2_EN
PC13.Signal=GPIO_Output
PC14-OSC32_IN.GPIO_Label=CAN1_EN
PC14-OSC32_IN.Signal=GPIO_Output
PC15-OSC32_OUT.GPIO_Label=POWER_5V
PC15-OSC32_OUT.Signal=GPIO_Output
PC2_C.Signal=SPI2_MISO
PC3_C.GPIO_Label=GYRO_CS
PC3_C.Signal=GPIO_Output
PC4.GPIO_Label=BAT
PC4.Signal=ADCx_INP4
PD0.Signal=FDCAN1_RX
PD1.Signal=FDCAN1_TX
PD12.Signal=FDCAN3_RX
PD13.Signal=FDCAN3_TX
PD2.Signal=UART5_RX
PE10.GPIO_Label=ACC_INT
PE10.Signal=GPXTI10
PE12.GPIO_Label=GYRO_INT
PE12.Signal=GPXTI12
PE7.Signal=UART7_RX
PE8.Signal=UART7_TX
PH0-OSC_IN.Signal=RCC_OSC_IN
PH1-OSC_OUT.Signal=RCC_OSC_OUT

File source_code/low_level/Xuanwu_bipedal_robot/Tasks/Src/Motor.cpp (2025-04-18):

#include "Motor.h"
#include "math.h"
#include "Robot_Types.h"
#include "cmsis_os.h"

Motor::Motor()
{
	motor_info[Left_Hip_Yaw].can_bus = 1;
	motor_info[Left_Hip_Yaw].id = 0x01;
	motor_info[Left_Hip_Yaw].ctrl.mode = 0; // 0: MIT, 1: Pos, 2: Vel
	motor_info[Left_Hip_Yaw].range = 0.5f;

	motor_info[Left_Hip_Roll].can_bus = 1;
	motor_info[Left_Hip_Roll].id = 0x02;
	motor_info[Left_Hip_Roll].ctrl.mode = 0;
	motor_info[Left_Hip_Roll].range = 0.7f;

	motor_info[Left_Hip_Pitch].can_bus = 1;
	motor_info[Left_Hip_Pitch].id = 0x03;
	motor_info[Left_Hip_Pitch].ctrl.mode = 0;
	motor_info[Left_Hip_Pitch].range = 1.5f;

	motor_info[Left_Knee_Pitch].can_bus = 1;
	motor_info[Left_Knee_Pitch].id = 0x04;
	motor_info[Left_Knee_Pitch].ctrl.mode = 0;
	motor_info[Left_Knee_Pitch].range = 1.5f;

	motor_info[Left_Ankle_Pitch].can_bus = 1;
	motor_info[Left_Ankle_Pitch].id = 0x05;
	motor_info[Left_Ankle_Pitch].ctrl.mode = 0;
	motor_info[Left_Ankle_Pitch].range = 1.5f;

	motor_info[Right_Hip_Yaw].can_bus = 2;
	motor_info[Right_Hip_Yaw].id = 0x21;
	motor_info[Right_Hip_Yaw].ctrl.mode = 0;
	motor_info[Right_Hip_Yaw].range = 0.5f;

	motor_info[Right_Hip_Roll].can_bus = 2;
	motor_info[Right_Hip_Roll].id = 0x22;
	motor_info[Right_Hip_Roll].ctrl.mode = 0;
	motor_info[Right_Hip_Roll].range = 0.7f;

	motor_info[Right_Hip_Pitch].can_bus = 2;
	motor_info[Right_Hip_Pitch].id = 0x23;
	motor_info[Right_Hip_Pitch].ctrl.mode = 0;
	motor_info[Right_Hip_Pitch].range = 1.5f;

	motor_info[Right_Knee_Pitch].can_bus = 2;
	motor_info[Right_Knee_Pitch].id = 0x24;
	motor_info[Right_Knee_Pitch].ctrl.mode = 0;
	motor_info[Right_Knee_Pitch].range = 1.5f;

	motor_info[Right_Ankle_Pitch].can_bus = 2;
	motor_info[Right_Ankle_Pitch].id = 0x25;
	motor_info[Right_Ankle_Pitch].ctrl.mode = 0;
	motor_info[Right_Ankle_Pitch].range = 1.5f;

	soft_start_flag = 0;
}

uint8_t Motor::returnZeroPos(uint8_t received_data_flag)
{
	all_joints_zeroed_flag = 1;
	for (int i = 0; i < NUM_MOTORS; i++)
	{
		motor_info[i].ctrl.pos_set = 0;
		motor_info[Left_Hip_Pitch].ctrl.pos_set = 0.152f;
		motor_info[Left_Knee_Pitch].ctrl.pos_set = -0.36f;
		motor_info[Left_Ankle_Pitch].ctrl.pos_set = 0.208f;
		motor_info[Right_Hip_Pitch].ctrl.pos_set = 0.152f;
		motor_info[Right_Knee_Pitch].ctrl.pos_set = -0.36f;
		motor_info[Right_Ankle_Pitch].ctrl.pos_set = 0.208f;
		
		motor_info[i].ctrl.kp_set = 20.0f;
		motor_info[i].ctrl.kd_set = 1.0f;
		
		if (fabs(motor_info[i].para.pos - motor_info[i].ctrl.pos_set) < 0.1f)
		{
			motor_info[i].reached_pos_flag = 1;
		}
		else
		{
			motor_info[i].reached_pos_flag = 0;
		}

		all_joints_zeroed_flag = all_joints_zeroed_flag && motor_info[i].reached_pos_flag;
	}

	if (all_joints_zeroed_flag && received_data_flag)
	{
		for (int i = 0; i < NUM_MOTORS; i++)
		{
			// motor_info[i].ctrl.kp_set = kps[i];
			// motor_info[i].ctrl.kd_set = kds[i];
			motor_info[i].ctrl.kp_set = 0.0f;
			motor_info[i].ctrl.kd_set = 0.0f;
		}
		return true;
	}

	return false;
}

void Motor::createVirtualBoundary(void)
{
	for (int i = 0; i < NUM_MOTORS; i++)
	{
		motor_info[i].ctrl.pos_set = (motor_info[i].ctrl.pos_set > motor_info[i].range) ? motor_info[i].range : motor_info[i].ctrl.pos_set;
		motor_info[i].ctrl.pos_set = (motor_info[i].ctrl.pos_set < -motor_info[i].range) ? -motor_info[i].range : motor_info[i].ctrl.pos_set;

		if (motor_info[i].para.pos > motor_info[i].range)
		{
			motor_info[i].ctrl.pos_set = motor_info[i].range - 0.1f;
			motor_info[i].ctrl.vel_set = 0;
			motor_info[i].ctrl.tor_set = 0;
			motor_info[i].ctrl.kp_set = 10;
			motor_info[i].ctrl.kd_set = 1;
		}
		else if (motor_info[i].para.pos < -motor_info[i].range)
		{
			motor_info[i].ctrl.pos_set = -motor_info[i].range + 0.1f;
			motor_info[i].ctrl.vel_set = 0;
			motor_info[i].ctrl.tor_set = 0;
			motor_info[i].ctrl.kp_set = 10;
			motor_info[i].ctrl.kd_set = 1;
		}
		else 
		{
			// motor_info[i].ctrl.kp_set = kps[i];
			// motor_info[i].ctrl.kd_set = kds[i];	
			motor_info[i].ctrl.kp_set = 0.0f;
			motor_info[i].ctrl.kd_set = 0.0f;
		}
	}
}

void Motor::resetJoints(void)
{
	disableAll();
	for (int i = 0; i < NUM_MOTORS; i++)
	{
		dm4310_clear_para(&motor_info[i]);
	}
	enableAll();
}

void Motor::sendAll(void)
{
	dm4310_ctrl_send(&motor_info[Left_Hip_Yaw]);
	dm4310_ctrl_send(&motor_info[Left_Hip_Roll]);
	delay_us(200);
	dm4310_ctrl_send(&motor_info[Left_Hip_Pitch]);
	dm4310_ctrl_send(&motor_info[Left_Knee_Pitch]);
	delay_us(200);
	dm4310_ctrl_send(&motor_info[Left_Ankle_Pitch]);
	dm4310_ctrl_send(&motor_info[Right_Hip_Yaw]);
	delay_us(200);
	dm4310_ctrl_send(&motor_info[Right_Hip_Roll]);
	dm4310_ctrl_send(&motor_info[Right_Hip_Pitch]);
	delay_us(200);
	dm4310_ctrl_send(&motor_info[Right_Knee_Pitch]);
	dm4310_ctrl_send(&motor_info[Right_Ankle_Pitch]);
	delay_us(200);
}

void Motor::disableAll(void)
{
	dm4310_disable(&motor_info[Left_Hip_Yaw]);
	dm4310_disable(&motor_info[Left_Hip_Roll]);
	delay_us(200);
	dm4310_disable(&motor_info[Left_Hip_Pitch]);
	dm4310_disable(&motor_info[Left_Knee_Pitch]);
	delay_us(200);
	dm4310_disable(&motor_info[Left_Ankle_Pitch]);
	dm4310_disable(&motor_info[Right_Hip_Yaw]);
	delay_us(200);
	dm4310_disable(&motor_info[Right_Hip_Roll]);
	dm4310_disable(&motor_info[Right_Hip_Pitch]);
	delay_us(200);
	dm4310_disable(&motor_info[Right_Knee_Pitch]);
	dm4310_disable(&motor_info[Right_Ankle_Pitch]);
	delay_us(200);
}

void Motor::enableAll(void)
{
	dm4310_enable(&motor_info[Left_Hip_Yaw]);
	dm4310_enable(&motor_info[Left_Hip_Roll]);
	delay_us(200);
	dm4310_enable(&motor_info[Left_Hip_Pitch]);
	dm4310_enable(&motor_info[Left_Knee_Pitch]);
	delay_us(200);
	dm4310_enable(&motor_info[Left_Ankle_Pitch]);
	dm4310_enable(&motor_info[Right_Hip_Yaw]);
	delay_us(200);
	dm4310_enable(&motor_info[Right_Hip_Roll]);
	dm4310_enable(&motor_info[Right_Hip_Pitch]);
	delay_us(200);
	dm4310_enable(&motor_info[Right_Knee_Pitch]);
	dm4310_enable(&motor_info[Right_Ankle_Pitch]);
	delay_us(200);
}

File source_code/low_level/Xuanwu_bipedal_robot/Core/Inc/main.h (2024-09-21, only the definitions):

#define CAN2_EN_Pin GPIO_PIN_13
#define CAN2_EN_GPIO_Port GPIOC
#define CAN1_EN_Pin GPIO_PIN_14
#define CAN1_EN_GPIO_Port GPIOC
#define POWER_5V_Pin GPIO_PIN_15
#define POWER_5V_GPIO_Port GPIOC
#define ACC_CS_Pin GPIO_PIN_0
#define ACC_CS_GPIO_Port GPIOC
#define GYRO_CS_Pin GPIO_PIN_3
#define GYRO_CS_GPIO_Port GPIOC
#define BAT_Pin GPIO_PIN_4
#define BAT_GPIO_Port GPIOC
#define ACC_INT_Pin GPIO_PIN_10
#define ACC_INT_GPIO_Port GPIOE
#define ACC_INT_EXTI_IRQn EXTI15_10_IRQn
#define GYRO_INT_Pin GPIO_PIN_12
#define GYRO_INT_GPIO_Port GPIOE
#define GYRO_INT_EXTI_IRQn EXTI15_10_IRQn
#define BUZZER_Pin GPIO_PIN_15
#define BUZZER_GPIO_Port GPIOB

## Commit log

2024-08-17 unified parts
    [0201_C.sldprt, 0201_R.sldprt, 0603_C.sldprt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]
2024-09-01 split parts for easier assembly and printing
    [6S Battery.SLDPRT, Battery Case Cap.SLDPRT, Battery Case.SLDPRT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]
2024-09-06 code started, IMU added and tested
    [Battery Case Cap.SLDPRT, Battery Case.SLDPRT, Central Connector Module Closing.SLDPRT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]
2024-09-09 DM4310 drivers added, fdcan bug fixed
    [DM4310driver.c, Motor.h, Xuanwu_bipedal_robot.ioc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]
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2024-09-14 Added virtual boundary and soft start for all motors, added CAN 2
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2024-09-16 forward kinematics using DH representation completed, can now compute end-effector (foot) position based on joint angles. inverse kinematics in progress
2024-09-20 Changed the compiler to ARM Compiler 6, changed freeRTOS to CMSIS_V2. Migrated most of the code to c++, improved code extendability and readability. Can successfully compile and execute like before.
2024-09-21 migrated almost all codes to c++, the current framework has some issues to be fixed tomorrow
    [BMI088driver.h, Debug.cpp, ET16S_Remote.cpp]
2024-09-21 Organized and moved all the tasks to one task file. The battery is completely drained as I forgot to turn off the robot yesterday, so I added battery level detection and system monitor to use buzzer 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
    [Debug.cpp, ET16S_Remote.cpp, Motor.cpp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]
2024-09-22 finished migrating all code to c++ (except for low level control code provided by motor manufacturer), solved the battery adc by a magic number, buzzer warning will give out when the battery is low
    [Robot.cpp, Task_Manager.cpp, Xuanwu_bipedal_robot.ioc]
2024-09-24 inverse kinematics correct, left leg verified
    [Battery Case Cap.SLDPRT, Battery Case.SLDPRT, Central Connector Module Closing.SLDPRT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]
2024-09-26 abandoning previous analytic inverse kinematics, using Newton Raphson numerical method instead. Code implemented in MATLAB
2024-09-28 Eigen Library added, Newton Raphson method for solving IK implemented, small errors to fix
    [Robot.cpp, Task_Manager.cpp]
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2024-09-29 inverse kinematic for x,y,z pos done, added remote watchdog, can now control left foot pos using remote
2024-10-05 inverse kinematic changed, now only solve for three joints to avoid having to do with pseudo inverse, yaw can now be controlled by hip yaw motor
    [Task_Manager.cpp]
2024-10-05 added mass properties to all the parts, corrected messy assembly to parts
    [0201_C.sldprt, 0201_R.sldprt, 0603_C.sldprt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]
2024-10-07 added dynamics calculation, CoM calculation completed and verified, ZMP calculation completed, need to go through again to verify
    [Foot_Connector.SLDPRT]
2024-10-08 added first order filter to IMU measurements, verified ZMP position to be correct
    [Task_Manager.cpp]
2024-10-19 found problem with CoM distribution, current CAD design is too wide for change of CoM, need to change CAD
    [Motor.cpp, Robot.cpp, Task_Manager.cpp]
2024-10-20 hip roll motor design changed
    [Central Connector Module.SLDPRT, DM-J4310 Hip Roll_Pitch Connector.SLDPRT, DM-J4310 Hip Roll_Pitch Connector_Lower.SLDPRT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]
2024-10-20 leg design changed, more modification to be made to improve movable angle and wiring
    [DM-J4310 Hip Pitch Connector.SLDPRT, DM-J4310 Hip Roll Connector.SLDPRT, DM-J4310 Hip Roll_Pitch Connector.SLDPRT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]
2024-10-29 CAD modified
    [DM-J4310 Hip Pitch Connector.SLDPRT, DM-J4310 Hip Roll Connector.SLDPRT, DM-J4310 Hip Yaw Connector.SLDPRT]
2024-10-30 model 2 CAD completed, modified overall width, added clearance to allow larger angle, allow easier installation and replacement now
    [Battery Case.SLDPRT, Central Connector Module Closing.SLDPRT, Central Connector Module.SLDPRT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]
2024-11-07 CAN communication between STM32 and Orin added, package not confirmed
    [DM-J4310 Hip Roll Connector Right 1.SLDPRT, DM-J4310 Hip Roll Connector Right 2.SLDPRT, DM-J4310 Hip Roll Connector Right.SLDPRT]
2024-11-09 CAN protocol with Orin NX established, not tested yet
    [Central Connector Module Closing.SLDPRT]
2024-11-19 fix(STM32 code base): fixed Orin communication and added corresponding freeRTOS task
    [Motor.h, Orin_Nx.cpp, Task_Manager.cpp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]
2024-11-19 feat(Orin): added and tested CAN communication with STM32, protocol not implemented yet
2024-11-22 fix(STM32): fixed CAN receive logic for Orin communication
    [Orin_Nx.cpp, Task_Manager.cpp]
2024-11-22 feat(Orin): CAN communication with STM32 tested to be successful, data decoded to be correct
2024-11-24 fix(Orin): changed variable structure for the robot for better readability and modularity
    [robot_configs.h]
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2024-11-25 feat(STM32): added watchdog mechanism for Orin communication, only send up receiving to avoid clogging Orin
    [Motor.cpp, Orin_Nx.cpp]
2024-11-25 test(Orin): tested motor control through Orin command, added shell script to autostart can0
2024-11-25 fix(Orin): removed sleep for 1 ms for CAN send and receive for optimal performance
    [xuanwu.cpp]
2024-11-29 test(Motors): corrected motor ID for version 2 CAD, tested all motor CAN communication, reset zero position
    [Motor.cpp, Task_Manager.cpp]
2024-12-02 refactor(MATLAB): added the method of Product of Exponentials for kinematics and tested the code
2024-12-02 feat(Orin): implemented inverse kinematics using ldlt decomposition to speed up computation and tested the result to be correct
    [robot.cpp, robot_configs.h, xuanwu.cpp]
2024-12-06 fix(MATLAB): fixed wrong result in CoM calculation
    [Task_Manager.cpp]
2024-12-07 fix(Orin): corrected ZMP calculation
    [xuanwu.cpp]
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2024-12-11 feat(Orin): tested center FK and IK, fixed IMU bug, tried CoM control but failed
    [robot.cpp, robot_configs.h]
2024-12-11 fix(STM32): fixed gyro unit error in Orin communication
    [Motor.cpp, Orin_Nx.cpp, Task_Manager.cpp]
2024-12-15 fix(MATLAB): fixed CoM forward and inverse kinematics
2024-12-16 fix(MATLAB): fixed CoM IK to be in the world frame
    [Task_Manager.cpp]
2024-12-17 feat(V3 CAD): added ankle joint motor, 5 DOF per leg now, modified motor PID
    [DM-J4310 Ankle Connector.SLDPRT, DM-J4310 Knee Pitch Connector.SLDPRT, Foot Connector.SLDPRT]
2024-12-17 test(Orin): ZMP static control doesn't seem to work
    [xuanwu.cpp]
2024-12-22 fix(CAD): fixed a minor dimensional mistake
    [Central Connector Module Closing.SLDPRT, DM-J4310 Ankle Connector 1.SLDPRT, DM-J4310 Ankle Connector 2.SLDPRT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]
2024-12-26 fix(STM32): installed two more motors for foot pitch, wired up and CAN ID have been updated, need to correct Orin protocol
    [Motor.cpp, Motor.h, Task_Manager.cpp]
2024-12-28 fix(STM32): Orin protocol fixed to include foot motors
    [Motor.cpp, Orin_Nx.cpp]
2024-12-28 fix(Orin): STM32 Communication fixed, data structure needs to be changed to accommodate foot motors
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2025-01-07 fix(MATLAB): fixed all MATLAB codes to include the ankle pitch motor
2025-01-08 fix(Orin): moved new kinematics code from MATLAB to Orin, both CoM IK FK and foot IK FK checked, more tests need to be done
    [robot.cpp, robot_configs.h, xuanwu.cpp]
2025-01-09 fix(Orin): tried to fix the jittering, however still cannot find the root cause, need further investigation
    [xuanwu.cpp]
2025-01-10 feat(MATLAB): foot inverse kinematics now solve for orientation as well! ready to be implemented
2025-01-11 feat(Orin): Successfully implemented IK with orientationgit add .! (MAN THIS IS HARD), tested and the self adaptability of foot wrt the ground
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2025-03-02 fix(STM32,MATLAB): fixed IMU raw accel filter, fixed MATLAB twist representation to [v;w] to be consistent with Mathematica and MLS book
2025-03-02 refractor(Orin): used Mathematica's kinematics result instead of MATLAB's as it simplifies further, computation time is slightly reduced
    [log.csv]
2025-03-02 fix(Orin): fixed new changes did not successfully pushed to remote
    [robot_configs.h, walking_patterns.h, xuanwu.cpp]
2025-03-03 feat(Orin): walking pattern using Kajita's LIPM tested, can now alternate between two legs, however, since there's no consideration for CoM transfer between legs, still cannot walk, need to implement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
    [log.csv]
2025-03-04 refactor(Orin): attempts to directly control ZMP through CoM Jacobian failed, refactored gaitPlanner, need to implement a better trajectory generator
    [log.csv]
2025-03-05 feat(Orin): implemented Cubic Bezier curve to smooth trajectory, need to shift weight more
    [log.csv]
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2025-03-06 fix(Orin): fixed foot wrench, changed pattern generation algorithm
    [log.csv]
2025-03-06 feat(Orin): added push off before foot swing, seemed to have some effect! Need more testing!
    [log.csv]
2025-03-07 feat(CAD): modified the robot design to reduce the distance between leg for easier weight shift
    [Central Connector Module.SLDPRT, DM-J4310 Hip Yaw Connector.SLDPRT]
2025-03-07 feat(Orin): changed joint length to adapt to the modification in CAD, ready for the second walking teest
    [log.csv]
2025-03-07 fix(Orin): tested, need to improve weight shift and check LIPM algorithm
    [walking_patterns.h, xuanwu.cpp]
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2025-03-08 feat(CAD): exported URDF file based on CAD, need to fix the inertia matrix
    [Battery Case Cap.SLDPRT, Battery Case.SLDPRT, Central Connector Module Closing.SLDPRT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]
2025-03-08 fix(URDF): fixed inertia matrix and mass properties
    [Full_Assem.SLDASM.urdf]
2025-03-08 feat(Mujoco): added urdf2xml conversion
    [Full_Assem.SLDASM.csv, Xuanwu.urdf, link_10.STL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]
2025-03-08 feat(Mujoco): added XML file and code for urdf2xml
    [Xuanwu.urdf, Xuanwu.xml, link_10.STL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]
2025-03-09 fix(Mujoco): fixed some minor details
    [Xuanwu.urdf, Xuanwu.xml, base_link.STL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]
2025-03-09 fix(Mujoco): fixed link position, inertia matrix, and mesh size, can now display normally in Mujoco
    [Xuanwu.urdf, Xuanwu.xml, base_link.STL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]
2025-03-10 fix(Mujoco): finally fixed the jittering issue with mesh internal collison by defining bounding box for each link
    [Xuanwu.xml]
2025-03-15 fix(Mujoco): fixed URDF properties to align with MJCF
    [Xuanwu.urdf]
2025-03-19 media(Sim2Sim): updated urdf and mjcf files, added Sim2Sim footage
    [Xuanwu.urdf, Xuanwu.xml]
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2025-03-25 feat(Orin): added lighter CAN package with STM32
    [log.csv]
2025-03-25 feat(STM32): added light package for CAN communication with Orin
    [DM-J4310 Foot Connector 1.SLDPRT, DM-J4310 Foot Connector 2.SLDPRT, Foot Connector.SLDPRT]
2025-03-26 feat(STM32): timed each task to make sure frequency is truly 1000Hz, found discritization noises when cmd passes from Orin to STM32, added low-pass filter to position cmd
    [Motor.cpp, Motor.h, Orin_Nx.cpp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]
2025-03-26 fix(STM32): changed stiffness for hip roll
    [Motor.cpp, Task_Manager.cpp]
2025-03-28 fix(URDF): fixed incorrect body mass due to calculation using density, the mass should hopefully be more correct
    [Battery Case Cap.SLDPRT, Battery Case.SLDPRT, Central Connector Module Closing.SLDPRT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]
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2025-03-31 feat(Orin): improved timeliness by introducing CPU locking and thread priority
    [log.csv]
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2025-04-02 docs: added testing result for commanded torque using pd control to compare with simulation
    [act_tor.csv]
2025-04-02 feat: added sim torque results, created a jupyter notebook for analyzing joint torque discrepancy
    [act_tor.csv, sim_tor.csv]
2025-04-08 feat(URDF): changed some mass properties to align with new 3D printed parts
    [Central Connector Module.SLDPRT, DM-J4310 Hip Roll Joint Board.SLDPRT, DM-J4310 Hip Yaw Connector.SLDPRT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]
2025-04-09 feat(RL): added new policy
    [Xuanwu.urdf]
2025-04-10 fix(URDF): corrected mass properties
    [DM-J4310 Hip Roll Connector Left.SLDPRT, Xuanwu.urdf, Xuanwu.xml]
2025-04-11 feat: finally fixed the bug of left leg tilting towards one side, new policy added for evaluation
    [tau_output.csv]
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2025-04-12 fix(STM32): changed back to position control mode as it shows better stability
    [Motor.cpp, Orin_Nx.cpp, Task_Manager.cpp]
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2025-04-18 feat(STM32): once again tuned PD for force control, now individual joint functions properly but together they still create vibrations
    [Motor.cpp, Orin_Nx.cpp, Task_Manager.cpp]
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2025-04-20 fix(Models): fixed URDF and MJCF based on true component measurements
    [DM-J4310 Foot Joint Board.SLDPRT, DM-J4310 Hip Pitch Connector.SLDPRT, DM-J4310 Hip Roll Connector Left.SLDPRT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]

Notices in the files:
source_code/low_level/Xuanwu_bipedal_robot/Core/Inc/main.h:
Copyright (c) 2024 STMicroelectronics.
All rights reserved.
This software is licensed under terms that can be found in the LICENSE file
